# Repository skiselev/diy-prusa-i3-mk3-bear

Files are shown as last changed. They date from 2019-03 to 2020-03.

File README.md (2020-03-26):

# diy-prusa-i3-mk3-bear
My attempt to build an improved Prusa i3 MK3 3D printer clone with Full Bear frame from scratch

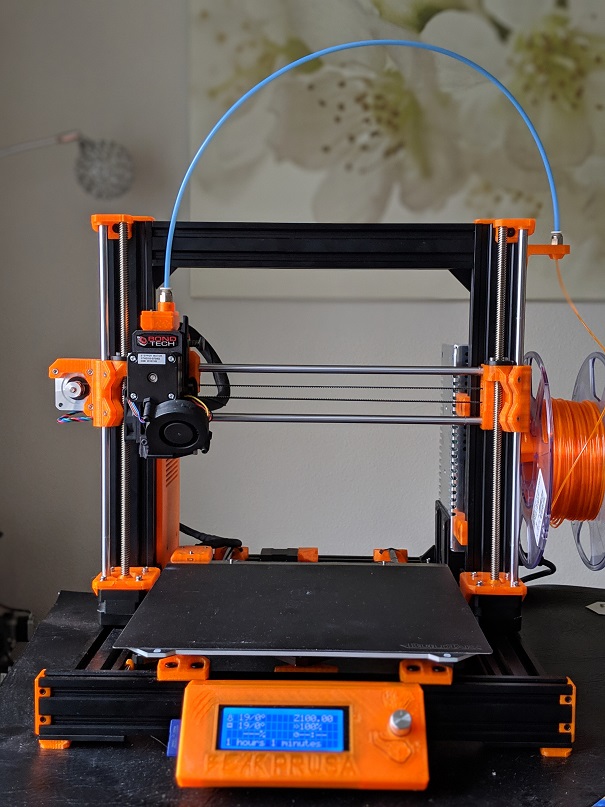
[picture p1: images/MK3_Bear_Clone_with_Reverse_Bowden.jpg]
MK3 Bear Clone with Reverse Bowden


## Building Instructions

### Procuring Parts and Materials

* Purchase the parts and the materials according to the [Bill of Materials](#bill-of-materials) section below
* Print required 3D printed tools and parts as listed below
  * Note the print priority:
    * Priority 1 parts are required for assembling the printer
    * Priority 2 parts are useful for continious printer operation
    * Priority 3 parts are not essential, mostly decorative parts
  * It is possible to print priority 2 and priority 3 parts once the printer is assembled, using the printer itself

### Building Steps

1. Follow the [Prusa i3 Bear Full Upgrade MK3 Assembly Instruction](https://github.com/gregsaun/prusa_i3_bear_upgrade/blob/master/full_upgrade/for_mk3/manual/assembly_instructions.md) steps 1 - 9 to assemble the v-slot frame, mount Y rods and Y motor
   * Note: The feet and the power supply lower mount can be installed later
   * Note: Use thread locker for metal thread to metal thread (not metal thread to plastic)
2. Follow the [Original Prusa i3 MK3S kit assembly guide - Y-axis assembly](https://manual.prusa3d.com/Guide/2.+Y-axis+assembly/1046?lang=en) steps 24 - 27 to assemble the Y carriage
   * Note: Lubricate linear bearings before installation
3. Follow the [Prusa i3 Bear Full Upgrade MK3 Assembly Instruction](https://github.com/gregsaun/prusa_i3_bear_upgrade/blob/master/full_upgrade/for_mk3/manual/assembly_instructions.md) step 10, bullets 1 - 5 to mount the Y carriage on the Y rods (330 mm)
   * Note: Do not follow the Y belt installation instructions - bullets 6 - 9
4. Follow the [Original Prusa i3 MK3S kit assembly guide - Y-axis assembly](https://manual.prusa3d.com/Guide/2.+Y-axis+assembly/1046?lang=en) steps 33 - 42 to assemble and tension the Y belt, and consume 15% of gummy bears
   * Note: All3D Makers MK3 Y carriage does not have threaded M3 holes for Y belt holder and tensioner. I had to use longer M3x14 mm screws and nylock nuts to secure these parts. Prusa MK3 uses M3x10mm screws instead.
5. Follow the [Bear Extruder And X Axis Assembly - X axis](https://guides.bear-lab.com/Guide/2.+X+axis/3) to build the X axis.
   * Note: Lubricate linear bearings before installation
6. Follow the [Prusa i3 Bear Full Upgrade MK3 Assembly Instruction](https://github.com/gregsaun/prusa_i3_bear_upgrade/blob/master/full_upgrade/for_mk3/manual/assembly_instructions.md) steps 11 - 13 to install Z motors and Z rods (320 mm), mount the X axis, and Z tops
7. Follow the [Bondtech for Prusa i3 - Assembly and Installation Manual](https://github.com/BondtechAB/Bondtech_Prusa_i3/blob/master/Doc/Assembly%20manual%20Bondtech_Prusa_i3_V1.1.pdf) to build the extruder and mount it on the X axis. Refer to [Bear X axis and Extruder - Bondtech Prusa Upgrade Extruder Assembly Guide](https://github.com/gregsaun/bear_extruder_and_x_axis/tree/master/optional_parts/bondtech_x_carriage) for X carriage mounting instructions and drawings. Install the X belt, and tighen it using two M3x18mm screws on X idler
8. Follow the [Original Prusa i3 MK3S kit assembly guide - Heatbed and PSU assembly](https://manual.prusa3d.com/Guide/7.+Heatbed++&+PSU+assembly+(Silver+PSU)/1051?lang=en) steps 1 - 17 to assemble the heatbed
9. (If priority 2 parts are available) Follow the [Prusa i3 Bear Full Upgrade MK3 Assembly Instruction](https://github.com/gregsaun/prusa_i3_bear_upgrade/blob/master/full_upgrade/for_mk3/manual/assembly_instructions.md) steps 14 and 15 to mount the LCD and the power supply unit.
   * Note: The LCD module I've got has a slightly bigger than standard PCB, and I had to file it to make it fit.
10. (If priority 2 parts are available) Follow the [Universal Zaribo Einsy Box](https://www.thingiverse.com/thing:3239428) instructions to install the Einsy Enclosure
    * Note: The Bear Einsy enclosure is slightly wider than it should be to fit properly. I had to file a corner to make it fit.
11. (If priority 3 parts are available) install end caps according to the [Prusa i3 Bear Full Upgrade MK3 Assembly Instruction](https://github.com/gregsaun/prusa_i3_bear_upgrade/blob/master/full_upgrade/for_mk3/manual/assembly_instructions.md) steps 14 and 19
12. Follow the [Original Prusa i3 MK3S kit assembly guide - Electronics assembly](https://manual.prusa3d.com/Guide/8.+Electronics+assembly/1052?lang=en) to wire the motors, the headbed, and the extruder to Einsy Rambo module.
13. (If priority 3 parts are available) route and secure the cables according to the [Prusa i3 Bear Full Upgrade MK3 Assembly Instruction](https://github.com/gregsaun/prusa_i3_bear_upgrade/blob/master/full_upgrade/for_mk3/manual/assembly_instructions.md) step 18
14. Perform the pre-flight check according to the [Original Prusa i3 MK3S kit assembly guide - Preflight check](https://manual.prusa3d.com/Guide/9.+Preflight+check/1053?lang=en)
15. Calibrate the printer according to the [Prusa i3 Bear Full Upgrade MK3 Assembly Instruction](https://github.com/gregsaun/prusa_i3_bear_upgrade/blob/master/full_upgrade/for_mk3/manual/assembly_instructions.md) steps 20 and 21.
16. (If priority 2 parts were not initially printed) Print priority 2 parts, and follow the steps 8 and 9 above to mount the LCD module, the power supply unit, and the Einsy enclosure.
17. (If priority 3 parts were not initially printed) Print priority 3 parts, and follow the steps 10 and 12 above to install end caps and route the wires

### Firmware
* Download [Bondtech Firmware Variation Updates For Prusa 3D Printers - For MK3S Using AllMetal V6](https://www.bondtech.se/en/knowledge-base/firmware-updates-for-prusa-i3/)
* Flash the firmware using PrusaSlicer *Configuration -> Flash printer firmware* menu

### MK3S Sensor Add-on

To be completed

### Reverse Bowden Add-on

To be completed

## Bill of Materials
Assembly/Component Type     | Description                       | Quantity | Price | Possible sources and notes
--------------------------- | --------------------------------- | -------- | ----- | -------------------------- 
Aluminum Frame and Hardware | Full Bear MK3 Upgrade Kit - [Detailed BOM](https://github.com/gregsaun/prusa_i3_bear_upgrade/blob/master/full_upgrade/for_mk3/manual/bom.md) | 1 | $124.99 |ALL3D Makers [MK3 Bear Upgrade](https://all3dmakers.com/collections/bear-upgrade-kit/products/mk3-bear-upgrade)
3D Printed Tool             | Full Bear MK3 - [build_helper_106mm](https://github.com/gregsaun/prusa_i3_bear_upgrade/blob/master/full_upgrade/for_mk3/printed_parts/stl/build_helper_106mm.stl) | 1 | Filament | Print (priority 1)
3D Printed Tool             | [Linear Bearing Greasing cap](https://www.thingiverse.com/thing:1128781) - [Linear_Bearing_Greaser_-_LM8UU](https://www.thingiverse.com/download:1772343) | 1 | Filament | Print (priority 1) 
3D Printed Tool             | Bondtech Extruder [PTFE Cutter 6.3 mm](https://github.com/BondtechAB/Bondtech_Prusa_i3/blob/master/CAD-Files/PTFE-CUTTER_1.0.STL) | 1 | Filament | Print (priority 1)
3D Printed Part             | Full Bear MK3 - [rod_holder](https://github.com/gregsaun/prusa_i3_bear_upgrade/blob/master/full_upgrade/for_mk3/printed_parts/stl/rod_holder.stl) | 4 | Filament | Print (priority 1)
3D Printed Part             | Full Bear MK3 - [y_idler_23](https://www.thingiverse.com/thing:3309424) | 1 | Filament | Print (priority 1). Note: 5 mm bore version for E3D 2GT 20T idler
3D Printed Part             | Full Bear MK3 - [y_motor_mount](https://github.com/gregsaun/prusa_i3_bear_upgrade/blob/master/full_upgrade/for_mk3/printed_parts/stl/y_motor_mount.stl) | 1 | Filament | Print (priority 1)
3D Printed Part             | Full Bear MK3 - [z_motor_mounts](https://github.com/gregsaun/prusa_i3_bear_upgrade/blob/master/full_upgrade/for_mk3/printed_parts/stl/z_motor_mounts.stl) | 1 (total of 2 parts) | Filament | Print (priority 1)
3D Printed Part             | Full Bear MK3 - [z_motor_mount_front](https://github.com/gregsaun/prusa_i3_bear_upgrade/blob/master/full_upgrade/for_mk3/printed_parts/stl/z_motor_mount_front.stl) | 2        | Filament | Print (priority 1)
3D Printed Part             | Full Bear MK3 - [z_tops](https://github.com/gregsaun/prusa_i3_bear_upgrade/blob/master/full_upgrade/for_mk3/printed_parts/stl/z_tops.stl) | 1 (total of 2 parts) | Filament | Print (priority 1)
3D Printed Part             | Full Bear MK3 - [foot](https://github.com/gregsaun/prusa_i3_bear_upgrade/blob/master/full_upgrade/for_mk3/printed_parts/stl/foot.stl) | 4 | Filament | Print (priority 2)
3D Printed Part             | Full Bear MK3 - [psu_lower_mount](https://github.com/gregsaun/prusa_i3_bear_upgrade/blob/master/full_upgrade/for_mk3/printed_parts/stl/psu_lower_mount.stl) | 1 | Filament | Print (priority 2)
3D Printed Part             | Full Bear MK3 - [psu_upper_mount](https://github.com/gregsaun/prusa_i3_bear_upgrade/blob/master/full_upgrade/for_mk3/printed_parts/stl/psu_upper_mount.stl) | 2 | Filament | Print (priority 2)
3D Printed Part             | Full Bear MK3 - [lcd_support_a](https://github.com/gregsaun/prusa_i3_bear_upgrade/blob/master/full_upgrade/for_mk3/printed_parts/stl/lcd_support_a.stl) | 1 | Filament | Print (priority 2)
3D Printed Part             | Full Bear MK3 - [lcd_support_b](https://github.com/gregsaun/prusa_i3_bear_upgrade/blob/master/full_upgrade/for_mk3/printed_parts/stl/lcd_support_b.stl) | 1 | Filament | Print (priority 2)
3D Printed Part             | Full Bear MK3 - [cable_clip_lcd](https://github.com/gregsaun/prusa_i3_bear_upgrade/blob/master/full_upgrade/for_mk3/printed_parts/stl/cable_clip_lcd.stl) | 6 | Filament | Print (priority 3)
3D Printed Part             | Full Bear MK3 - [cable_clip_round](https://github.com/gregsaun/prusa_i3_bear_upgrade/blob/master/full_upgrade/for_mk3/printed_parts/stl/cable_clip_round.stl) | 5 | Filament | Print (priority 3)
3D Printed Part             | Full Bear MK3 - [cable_clip_ziptie](https://github.com/gregsaun/prusa_i3_bear_upgrade/blob/master/full_upgrade/for_mk3/printed_parts/stl/cable_clip_ziptie.stl) | 3 | Filament | Print (priority 3)
3D Printed Part             | Full Bear MK3 - [end_caps](https://github.com/gregsaun/prusa_i3_bear_upgrade/blob/master/full_upgrade/for_mk3/printed_parts/stl/end_caps.stl) | 2 (total of 4 parts) | Filament | Print (priority 3)
3D Printed Part             | Full Bear MK3 - [end_cap_z_axis](https://github.com/gregsaun/prusa_i3_bear_upgrade/blob/master/full_upgrade/for_mk3/printed_parts/stl/end_cap_z_axis.stl) | 2 | Filament | Print (priority 3)
3D Printed Part             | Bear Extruder and X Axis MK3 - [x_carriage](https://github.com/gregsaun/bear_extruder_and_x_axis/blob/master/printed_parts/stl/mk3/x_carriage.stl) | 1 | Filament | Print (priority 1)
3D Printed Part             | Bear Extruder and X Axis MK3 - [x_end_motor](https://github.com/gregsaun/bear_extruder_and_x_axis/blob/master/printed_parts/stl/mk3/x_end_motor.stl) | 1 | Filament | Print (priority 1)
3D Printed Part             | Bear Extruder and X Axis MK3 - [x_end_idler](https://github.com/gregsaun/bear_extruder_and_x_axis/blob/master/printed_parts/stl/common_to_all_versions/x_end_idler.stl) | 1 | Filament | Print (priority 1)
3D Printed Part             | Bear Extruder and X Axis MK3 - [x_end_idler_idler_mount](https://www.thingiverse.com/thing:3308226/files) | 1 | Filament | Print (priority 1). Note: 5 mm bore version for E3D 2GT 20T idler
3D Printed Part             | Bear Extruder and X Axis MK3 - [cable_guide_back_a](https://github.com/gregsaun/bear_extruder_and_x_axis/blob/master/printed_parts/stl/common_to_all_versions/cable_guide_back_a.stl) | 1 | Filament | Print (Priority 1).
3D Printed Part             | Bear Extruder and X Axis MK3 - [cable_guide_back_b](https://github.com/gregsaun/bear_extruder_and_x_axis/blob/master/printed_parts/stl/common_to_all_versions/cable_guide_back_b.stl) | 1 | Filament | Print (Priority 1).
3D Printed Part             | Bear Extruder and X Axis MK3 - [bondtech_x_carriage_mk3](https://github.com/gregsaun/bear_extruder_and_x_axis/blob/master/optional_parts/bondtech_x_carriage/printed_parts/bondtech_x_carriage_mk3.stl) | 1 | Filament | Print (priority 1)
3D Printed Part             | Bear Extruder and X Axis MK3 - [x_carriage_back](https://github.com/gregsaun/bear_extruder_and_x_axis/blob/master/printed_parts/stl/mk3/x_carriage_back.stl) | 1 | Filament | Print (priority 1)
3D Printed Part             | Bondtech Extruder [MK3S Sensor Add-on](https://github.com/BondtechAB/Bondtech_Prusa_i3/tree/master/CAD-Files/MK3s%20Sensor%20Add-On) | 1 | Filament | Print (priority 3)
3D Printed Part             | Original Prusa i3 MK3S - [y-belt-holder](https://github.com/prusa3d/Original-Prusa-i3/blob/MK3S/Printed-Parts/STL/y-belt-holder.stl) | 1 | Filament | Print (priority 1)
3D Printed Part             | Original Prusa i3 MK3S - [y-belt-tensioner](https://github.com/prusa3d/Original-Prusa-i3/blob/MK3S/Printed-Parts/STL/y-belt-tensioner.stl) | 1 | Filament | Print (priority 1)
3D Printed Part             | Original Prusa i3 MK3S - [z-screw-cover](https://github.com/prusa3d/Original-Prusa-i3/blob/MK3S/Printed-Parts/STL/z-screw-cover.stl) | 2 | Filament | Print (priority 1)
3D Printed Part             | Original Prusa i3 MK3S - [plug-aligner](https://github.com/prusa3d/Original-Prusa-i3/blob/MK3S/Printed-Parts/STL/plug-aligner.stl) | 1 | Filament | Print (priority 3)
3D Printed Part             | [Universal Zaribo Einsy Box](https://www.thingiverse.com/thing:3239428) - [021._MK3_Bear_Einsy_Body_NO_RASP_v5.stl](https://www.thingiverse.com/download:6151820) | 1 | Filament | Print (priority 2)
3D Printed Part             | [Universal Zaribo Einsy Box](https://www.thingiverse.com/thing:3239428) - [020._MK3_Bear_Einsy_Cover_NO_RASP_v5.stl](https://www.thingiverse.com/download:6049099) | 1 | Filament | Print (priority 2)
3D Printed Part             | [Universal Zaribo Einsy Box](https://www.thingiverse.com/thing:3239428) - [EinsyBox-CableCover1-2x.stl](https://www.thingiverse.com/download:5659498) | 2 | Filament | Print (priority 2)
3D Printed Part             | [Universal Zaribo Einsy Box](https://www.thingiverse.com/thing:3239428) - [EinsyBox-CableCover2-1x.stl](https://www.thingiverse.com/download:5659499) | 1 | Filament | Print (priority 2)
3D Printed Part             | [LCD Cover for Prusa Bear Upgrade](https://www.thingiverse.com/thing:3385560) | 1 | Filament | Print (priority 2). Alternatives: Original Prusa i3 MK3S - [LCD cover; LCD knob](https://github.com/prusa3d/Original-Prusa-i3/tree/MK3S/Printed-Parts/STL), or [Prusa Bear LCD cover](https://www.thingiverse.com/thing:2941711)
3D Printed Part             | Original Prusa i3 MK3S - [Heatbed cable cover](https://github.com/prusa3d/Original-Prusa-i3/blob/MK3S/Printed-Parts/STL/heatbed-cable-cover.stl) | 1 | Filament | Print (priority 1)
Bearing                     | LMU8 Linear Bearing               | 10 | $55.50| Misumi [LMU8](https://us.misumi-ec.com/vona2/detail/110300026540/?ProductCode=LMU8)
Metal Rod                   | Z-Axis Rod - 8 mm diameter, 320 mm length  | 2 | $24 | Misumi [PSFJ8-320](https://us.misumi-ec.com/vona2/detail/110302634310/?ProductCode=PSFJ8-320)
Metal Rod                   | Y-Axis Rod - 8 mm diameter, 330 mm length  | 2 | $24 | Misumi [PSFJ8-330](https://us.misumi-ec.com/vona2/detail/110302634310/?ProductCode=PSFJ8-330)
Metal Rod                   | Z-Axis Rod - 8 mm diameter, 370 mm length  | 2 | $24 | Misumi [PSFJ8-370](https://us.misumi-ec.com/vona2/detail/110302634310/?ProductCode=PSFJ8-370)
Belt                        | 2GT Belt                          | 2 | $14.54 | Misumi [GBN8522GT-60](https://us.misumi-ec.com/vona2/detail/110302652060/?ProductCode=GBN8522GT-60)
Idler                       | 2GT 20 Tooth Idler, 6 mm width, 5 mm bore     | 2 | £10.40 | E3D [M-IDLER-T-GT2-P20-6-A-P5-H100](https://e3d-online.com/gates-powergripr-toothed-idler-6mm)
Pulley                      | 2GT 16 Tooth Pulley, 6 mm width, 5 mm bore    | 2 | £7.00 | E3D [M-PULLEY-GT2-16T-6-P5-C-H155](https://e3d-online.com/gates-powergrip-pulley-16-tooth-6mm)
Dowel Pin                   | Dowel Pin 15.8 mm length, 5mm diameter | 2 | $1.69 | All3D Makers [Bear X Axis Dowel Pin for E3D Gates 5mm bore idler](https://all3dmakers.com/collections/hardware/products/bear-x-axis-dowel-pin-for-e3d-gates-5mm-bore-idler)
Electronics Assembly        | Einsy Rambo 1.1                   | 1 | $120.00 | UltiMachine [EINSY RAMBo 1.1](https://ultimachine.com/collections/electronics/products/einsy-rambo-1-1), All3D Makers [MK3 EINSY RAMBo](https://all3dmakers.com/collections/electronics/products/mk3-einsy-rambo)
Electronics Assembly        | 2004 LCD Display - [RepRapDiscount Smart Controller](https://reprap.org/wiki/RepRapDiscount_Smart_Controller) | 1 | $18.49 | All3D Makers [MK3/MK2.5/MK2 LCD Display](https://all3dmakers.com/collections/electronics/products/2004-reprap-lcd-display)
Fan                         | Print cooling fan | 1 | $8.69 | All3D Makers [MK3 Part Cooling Fan](https://all3dmakers.com/collections/electronics/products/mk3-part-cooling-fan)
Fan                         | Hotend fan | 1 | $13.69 | All3D Makers [Sunon MF40100V1-1000U-G99 Hotend Cooling Fan](https://all3dmakers.com/collections/electronics/products/sunon-mf40100v1-1000u-g99-hotend-cooling-fan)
Electronics Assembly        | PINDA 2 sensor | 1 | $15.99 | All3D Makers [P.I.N.D.A 2 Inductive Sensor](https://all3dmakers.com/collections/electronics/products/p-i-n-d-a-2-inductive-sensor)
Electronics Assembly        | Filament sensor | 1 | $11.69 | All3D Makers [MK3S IR Sensor Kit for New Bear Extruder](https://all3dmakers.com/collections/electronics/products/mk3s-ir-sensor-kit-for-new-bear-extruder)
Heatbed                     | MK52 headbed | 1 | $68 | 3DPrintronics [MK52 Heat bed for Prusa MK3](https://www.3dprintronics.com/Prusa-i3-Mk52-Heated-Bed-p101073046). Note: Order 24V version with mounting hardware and thermistor. Optionally order MK3 Y carriage ($24), PINDA 2 sensor ($11), and Spring Steel Sheet ($45). 
Electronics Assembly        | MK3 24V Power Supply | 1 | $69.99 | All3D Makers [24V MK3 Power Supply Assembly with Power Panic](https://all3dmakers.com/collections/electronics/products/24v-250-watts-switching-power-supply)
Motors kit                  | Stepper motors kit | 1 | $124.99 | All3D Makers [Motor Kit for Bear Upgrade, MK2/3, Haribo and Zaribo Mod](https://all3dmakers.com/collections/electronics/products/motor-kit-for-bear-upgrade-mk2-3-and-haribo-mod)
Aluminum Y carriage         | Prusa i3 MK3 Aluminum Y carriage | 1 | $38.99 | All3D Makers [Prusa i3 MK3 Aluminum Y carriage](https://all3dmakers.com/collections/hardware/products/original-prusa-i3-mk3-3d-printer-aluminum-y-carriage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)
Spring Steel Sheet          | MK3 Spring Steel Sheet | 1 | $25.75 | BuildTak [FlexPlate MK3 - 9.5"x10"](https://www.buildtak.com/product/flexplate-surface/)
Print Surface               | Print Surface | 1 | $14.25 | BuiltTak [Original 3D Printing Surface - 9"X10"](https://www.buildtak.com/product/buildtak-3d-printing-surface/)
Miscellanous Hardware       | U-Bolts for LMU8U Bearings and nyloc nuts | 1 set | $7.69 | All3D Makers [U-Bolts for LMU8U Bearings](https://all3dmakers.com/collections/hardware/products/u-bolts-to-hold-the-lm8uu-bearings-to-the-y-carriage-on-the-mk2s)
Miscellanous Hardware       | Textile sleeves for headbed and extruder cables | 1 set | $5.69 | All3D Makers [MK3/MK2.5 Heatbed and Extruder Textile Sleeve](https://all3dmakers.com/collections/hardware/products/mk3-mk2-5-heatbed-and-extruder-textile-sleeve)
Miscellanous Hardware       | 3 mm x 50 cm Nylon Filament | 1 | $0.69 | All3D Makers [MK3/MK2.5/MK2S Extruder Nylon Guide](https://all3dmakers.com/collections/hardware/products/mk3-mk2-5-mk2s-extruder-nylon-guide)
Extruder                    | [Bondtech MK2/MK2S/MK3 upgrade kit with Bondtech gears](https://www.bondtech.se/en/product/prusa-i3-mk2-mk2s-extruder-upgrade/) | 1 | $115 | All3D makers [Prusa i3 MK2/MK2S Extruder Upgrade](https://all3dmakers.com/collections/electronics/products/prusa-i3-mk2-mk2s-extruder-upgrade)
Hotend                      | E3D V6, 1.75 mm nozzle, 24V | 1 | £43.00, $79.99| E3D [V6-175-24V](https://e3d-online.com/v6-all-metal-hotend), All3D Makers [MK3 E3DV6 Assembled Hotend](https://all3dmakers.com/collections/electronics/products/mk3-e3dv6-assembled-hotend)
Screw                        | M4 x 10mm button socket screw | 2 | $0.42 | Fastenal [MB2530010A20000](https://www.fastenal.com/products/details/MB2530010A20000)<br>2 - power supply upper mount
Screw                        | M3 x 8mm socket cap screw    | 6 | $1.06 | Fastenal [MS2510008A20000](https://www.fastenal.com/products/details/MS2510008A20000)<br>6 - Einsy enclosure
Screw                        | M3 x 10mm socket cap screw    | 32 | $5.91 | Fastenal [MS2510010A20000](https://www.fastenal.com/products/details/MS2510010A20000)<br>3 - Y motor mount<br>2 - Y belt holder and tensioner<br>2 - headbed cable assembly<br>3 - headbed cable cover<br>6 - X end motor and idler<br>6 - X carriage<br>8 - Einsy enclosure<br>2 - LCD enclosure
Screw                        | M3 x 12mm socket cap screw    | 8 | $1.67 | Fastenal [MS2510012A20000](https://www.fastenal.com/products/details/MS2510012A20000)<br>8 - Z motor mounts
Screw                        | M3 x 14mm socket cap screw    | 2 | $0.18 | Fastenal [MS2510014A20000](https://www.fastenal.com/products/details/MS2510014A20000)<br>2 - Y belt holder and tensioner
Screw                        | M3 x 18mm socket cap screw    | 13 | $5.89 | Fastenal [MS2510018A20000](https://www.fastenal.com/products/details/MS2510018A20000)<br>9 - X end motor and idler<br>3 - X carriage<br>1 - power supply lower mount
Screw                        | M3 x 30mm socket cap screw    | 1 | $0.32 | Fastenal [MS2510030A20000](https://www.fastenal.com/products/details/MS2510030A20000)<br>1 - Y belt holder and tensioner
Screw                        | M3 x 40mm socket cap screw    | 4 | $1.45 | Fastenal [MS2510040A20000](https://www.fastenal.com/products/details/MS2510040A20000)<br>4 - X carriage
Nut                          | M3 hex nut                    | 27 | $1.98 | Fastenal [MN2510000A20000](https://www.fastenal.com/products/details/MN2510000A20000)<br>2 - Y belt holder and tensioner<br>3 - headbed cable cover<br>3 - X carriage<br>8 - X end motor and idler<br>10 - Einsy enclosure<br>1 - power supply lower mount
Nut                          | M3 nyloc nut                  | 7 | $1.12| Fastenal [1L2510000A20000](https://www.fastenal.com/products/details/1L2510000A20000)<br>3 - Y belt holder and tensioner<br>2 - headbed cable assembly<br>2 - X end idler mount
Nut                          | M3 square nut                 | 8 | $1.60 | Fastenal [0161907](https://www.fastenal.com/products/details/0161907)<br>4 - X carriage<br>4 - Einsy Enclosure
Washer                       | M3 x 7 mm washer              | 10 | $0.32 | Fastenal [MW6330000A20000](https://www.fastenal.com/products/details/MW6330000A20000)<br>8 - Z motor mounts<br>2 - headbed cable assembly
Filament                     | 1 kg PETG                     | 1 | $24.99 | Amazon [eSUN 3D 1.75mm PETG Orange Filament 1kg](https://www.amazon.com/eSUN-1-75mm-Filament-Printer-Semi-Transparent/dp/B010Y25QZ2)
Lubricant                    | Super Lube 21030 Synthetic Grease | 1 | $4.69 | Amazon [Super Lube 21030 Synthetic Grease (NLGI 2), 3 oz Tube](https://www.amazon.com/Super-Lube-21030-Synthetic-Grease/dp/B000XBH9HI)
Thread Locker                | Medium Strength (Blue) Thread Locker | 1 | $5.57 | Amazon [Vibra-TITE 121 Medium Strength Removable Anaerobic Threadlocker, 10ml Bottle, Blue](https://www.amazon.com/gp/product/B0025PSNKM)

### Reverse Bowden Add-on
Assembly/Component Type     | Description                       | Quantity | Price | Possible sources and notes
--------------------------- | --------------------------------- | -------- | ----- | --------------------------
3D Printed Part             | [Bondtech extruder add-on](https://www.thingiverse.com/thing:3463618) - [Sensor_Body_Bowden.stl](https://www.thingiverse.com/download:6144709) | 1 | Filament | Print
3D Printed Part             | [Bondtech-Prusa_i3_MK3S-Reverse_Bowden-Sensor_Cover.stl](printed_parts/Bondtech-Prusa_i3_MK3S-Reverse_Bowden-Sensor_Cover.stl) | 1 | Filament | Print
3D Printed Part             | [Lever.STL](https://github.com/BondtechAB/Bondtech_Prusa_i3/blob/master/CAD-Files/MK3s%20Sensor%20Add-On/Lever.STL) | 1 | Filament | Print
3D Printed Part             | Bear Extruder and X Axis MK3 [vslot_mount_pc4-m10](https://github.com/gregsaun/bear_extruder_and_x_axis/blob/master/optional_parts/reverse_bowden/printed_parts/vslot_mount_pc4-m10.stl) | 1 | Filament | Print
3D Printed Part             | [Spool Holder for 20mm V-Slot](https://www.thingiverse.com/thing:1625705) | 1 | Filament | Print
Hardware                    | PTFE Tubing - 1.75 mm x 1 meter<br>PC4-M10*0.9 Straight-Thru Fittings x2 | 1 set       | $15.99 | Capricorn Premium Bowden Tubing [SKU 2001](https://www.captubes.com/shop/#!/1-Meter-TL-Translucent-1-75mm-Bowden-Tubing/p/82190771/category=23214268)<br>Note: When at tubing page, add fittings from the drop down list on the right.
Screw                        | M3 x 16mm socket cap screw       | 1        | $0.11 | Fastenal [MS2510016A20000](https://www.fastenal.com/products/details/MS2510016A20000)

### Alternative: Original Prusa i3 MK3S Einsy Enclosure
Assembly/Component Type     | Description                       | Quantity | Price | Possible sources and notes
--------------------------- | --------------------------------- | -------- | ----- | -------------------------- 
3D Printed Part             | Full Bear MK3 - [rambo_base_lower_mount](https://github.com/gregsaun/prusa_i3_bear_upgrade/blob/master/full_upgrade/for_mk3/printed_parts/stl/rambo_base_lower_mount.stl) | 1 | Filament | Print (priority 3)
3D Printed Part             | Full Bear MK3 - [rambo_base_upper_mount](https://github.com/gregsaun/prusa_i3_bear_upgrade/blob/master/full_upgrade/for_mk3/printed_parts/stl/rambo_base_upper_mount.stl) | 1 | Filament | Print (priority 3)
3D Printed Part             | Full Bear MK3 - [rambo_lid_lower_hinge](https://github.com/gregsaun/prusa_i3_bear_upgrade/blob/master/full_upgrade/for_mk3/printed_parts/stl/rambo_lid_lower_hinge.stl) | 1 | Filament | Print (priority 3)
3D Printed Part             | Full Bear MK3 - [rambo_lid_upper_hinge](https://github.com/gregsaun/prusa_i3_bear_upgrade/blob/master/full_upgrade/for_mk3/printed_parts/stl/rambo_lid_upper_hinge.stl) | 1 |  Filament |Print (priority 3)
3D Printed Part             | Original Prusa i3 MK3S - [Einsy-base](https://github.com/prusa3d/Original-Prusa-i3/blob/MK3S/Printed-Parts/STL/Einsy-base.stl) | 1 | Filament | Print (priority 3)
3D Printed Part             | Original Prusa i3 MK3S - [Einsy-doors](https://github.com/prusa3d/Original-Prusa-i3/blob/MK3S/Printed-Parts/STL/Einsy-doors.stl) | 1 | Filament | Print (priority 3)
3D Printed Part             | Original Prusa i3 MK3S - [Extruder-cable-clip](https://github.com/prusa3d/Original-Prusa-i3/blob/MK3S/Printed-Parts/STL/Extruder-cable-clip.stl) | 1 | Filament | Print (priority 3)
3D Printed Part             | Original Prusa i3 MK3S - [Heatbed-cable-clip](https://github.com/prusa3d/Original-Prusa-i3/blob/MK3S/Printed-Parts/STL/Heatbed-cable-clip.stl) | 1 | Filament | Print (priority 3)

## Documentation

* [Prusa i3 Bear Full Upgrade MK3](https://github.com/gregsaun/prusa_i3_bear_upgrade/tree/master/full_upgrade/for_mk3/manual)
* [Original Prusa i3 MK3S Kit Assembly Manual](https://manual.prusa3d.com/c/Original_Prusa_i3_MK3S_kit_assembly)
* [Bondtech Prusa i3 Assembly Manual](https://github.com/BondtechAB/Bondtech_Prusa_i3/blob/master/Doc/Assembly%20manual%20Bondtech_Prusa_i3_V1.1.pdf)
* [Bondtech Prusa i3 - MK3S Sensor Add-On](https://github.com/BondtechAB/Bondtech_Prusa_i3/blob/master/Doc/Sensor%20Add-On%20V1.0.pdf)
* [Bear X Axis and Bondtech Extruder](https://github.com/gregsaun/bear_extruder_and_x_axis/tree/master/optional_parts/bondtech_x_carriage)
* [Optional part for Prusa i3 Bear Upgrade](https://github.com/gregsaun/prusa_i3_bear_upgrade/blob/master/optional_parts.md)
* [Regular extruder temperature drops with firmwares 3.5.0 and 3.5.1](https://github.com/prusa3d/Prusa-Firmware/issues/1405)

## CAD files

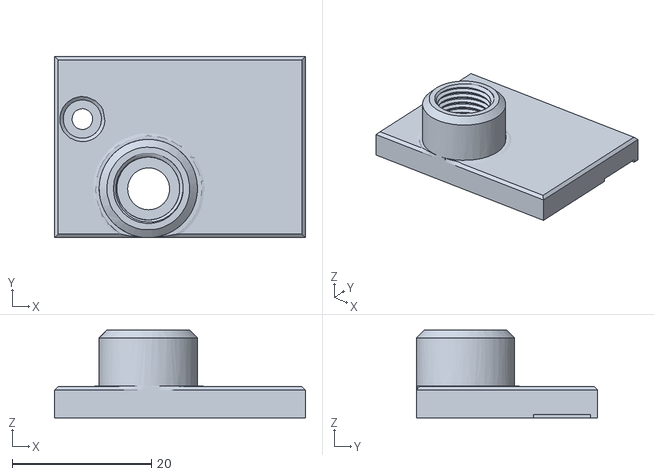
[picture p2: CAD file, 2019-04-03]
printed_parts/Bondtech-Prusa_i3_MK3S-Reverse_Bowden-Sensor_Cover.stl
36.0 x 26.0 x 12.6

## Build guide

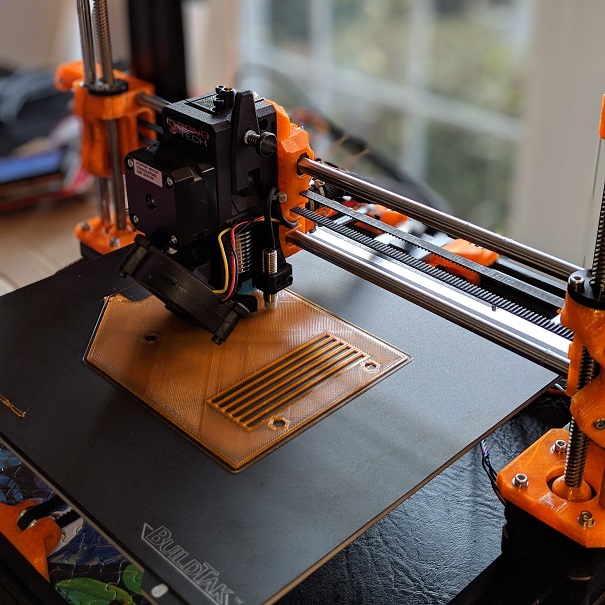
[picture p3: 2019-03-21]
images/MK3_Bear_Clone_Printing.jpg

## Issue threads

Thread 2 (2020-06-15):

Broken links

polyglotte, 2020-06-15:
Hi, I was checking some stl links for building this printer and some of them are broken, could you upload them again?

skiselev, 2020-06-15:
Can you please point out which links specifically?
Also note that Prusa/Bear project is constantly updating. So please follow the Bear project instructions. My instructions are more of the recommendations for building a printer from scratch vs. purchasing Prusa MK3S and upgrading it.

polyglotte, 2020-06-16:
the X axis and carriage links, thank's
I'm also making one from scratch, I don't even own a 3d printer yet, looking for a nice Fablab/Hackerspace/hearted person to print my parts.

Closed 2020-06-16.

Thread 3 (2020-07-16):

LCD not working?

Schmools, 2020-07-16:
Hi, thanks for the great documentation of your build. I've followed what you did and have 95% of everything assembled, however my LCD doesn't turn on at all, though if I mess with the knob the backlight sometimes flickers and the piezo beeps. Was wondering if you experienced anything similiar in your build process, and if that was the case how you remedied that. Thanks again for the great documentation!

elpeter25, 2020-08-04:
Just in case... did you try to switch the LCD cable? that works on other printers with non standard LCDs

Schmools, 2020-08-04:
Yeah, messed with it for a day or so and it turns out if you just buy one of the reprap displays arbitrarily, you have to be careful because the cables defaultly can come backwards, so you need to file down the tabs on the connectors to install them backwards.

elpeter25, 2020-08-05:
Actually you can just take out the plastic from the pcb with a pair of pliers and mount it back reverted.

Closed 2020-08-04.

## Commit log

2019-02-12 Add missing links, Add extruder and hotend
2019-02-12 Clarify Assembly/Component type and Description
2019-02-12 Add hardware: screws, nuts, washers
2019-02-12 Add prices; add filament
2019-02-12 Spelling fixes; add price for extruder
2019-02-15 Use MK3S y-belt-holder and y-belt-tensioner
2019-02-15 Add M3 x 30mm screw - used in Y belt tensioner
2019-02-15 Add z-screw-cover
2019-03-06 Add hardware for MK3S Y belt holder
2019-03-07 Cable guides are needed for Bondtech carriage
2019-03-07 Update link to headbed-cable-cover.stl
2019-03-15 README: Use bear alternatives for LCD and Einsy enclosures
2019-03-15 README: Add MK3S filament sensor; Update headbed source
2019-03-15 README: Add headbed and extruder cables hardware
2019-03-15 README: Move Original Prusa i3 MK3S Einsy enclosure into a separate section
2019-03-15 README: Add a detailed list of Einsy enclosure parts
2019-03-19 README: Add hardware for Einsy enclosure
2019-03-19 README: Add 3D printed tools
2019-03-20 README: Add assembly instructions section, update priority for non-essential parts
2019-03-20 README: Add assembly steps
2019-03-21 README: Update hotend fan and LCD to All3D Makers parts
2019-03-21 README: Add printer's photo
2019-03-21 README: Add grease and thread locker
2019-03-21 README: Add note about lubricating the bearings, add note about Y belt mounting holes, renumber assembly steps
2019-03-21 Add printer photo
2019-04-03 README: Add screw for MK3S sensor cover
2019-04-03 printed_parts: Add MK3S reverse bowden sensor cover
    [Bondtech-Prusa_i3_MK3S-Reverse_Bowden-Sensor_Cover.stl]
2019-04-03 README: Update picture to complete printer
2019-04-03 README: Add x_end_motor.stl
2019-04-13 README: Update the quantity and the price of M3 x 12 screws
